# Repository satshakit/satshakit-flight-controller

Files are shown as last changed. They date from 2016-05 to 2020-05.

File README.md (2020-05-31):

<h1 style="font-family: courier;" align="center"> satshakit flight controller</h1>
<p align="center">
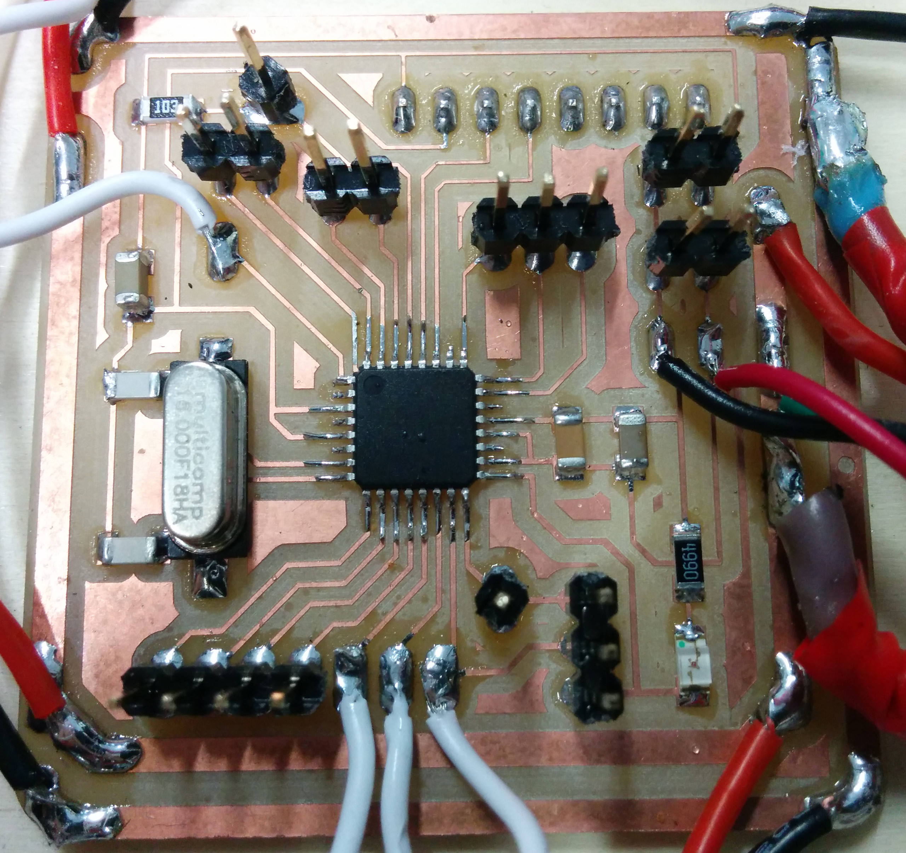
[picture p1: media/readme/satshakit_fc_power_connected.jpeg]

<div align="center"><i>An open source & easy to make flight controller board.</i></div>
</p>  

satshakit flight controller
--
satshakit flight controller is an **open source, MultiWii compatible, flight controller board**, that is possibile to **make in a FabLab**. The design derives from both a **satshakit board** and dual processor flight controller of my **[FabAcademy2015 final project](http://fabacademy.org/archives/2015/eu/students/ingrassia.daniele/index.html)**.

Here you can find all of the satshakit boards: **[satshakit organization](https://github.com/satshakit)**.

Features
--

satshakit flight controller has been designed aiming to be **easy to make, program and use**, so to be possible to **replicate and customize it** in any other Fab Lab. It has the following features:

- support for [any drone configuration](http://www.multiwii.com/connecting-elements) up to **8 motors**
- support for up to **6 channels** receivers 
- costs about **8€**
- **16mhz crystal** for precise clock, reliability and compatibility
- size of **48x48mmm** to fit the size of commercial available boards
- embedded **power board** (if needed)
- possibility to connect and use **any IMU working at 5V**

You can use satshakit flight controller in **DIY drones** or, due the dimensions are the same or less of most of the MultiWii commercial flight controller boards (50x50mmm), as a **replacement flight controller for commercial drones**. For drones up to 4 motors and 15A ESCs, is possible to use the **embedded power board**, otherwise is recommended to use an external power board, and to make the satshakit flight controller without the power board embedded.

Getting started
--

After you finish to solder a satshakit flight controller board, you need to **set its fuses and to program it with MultiWii**. To set the fuses you can easily upload the Arduino Bootloader using Arduino IDE and an **Arduino as ISP**. To do so first upload the Arduino as ISP sketch into an Arduino, and then connect the satshakit flight controller as following (this is the same for the version with the power board and without):

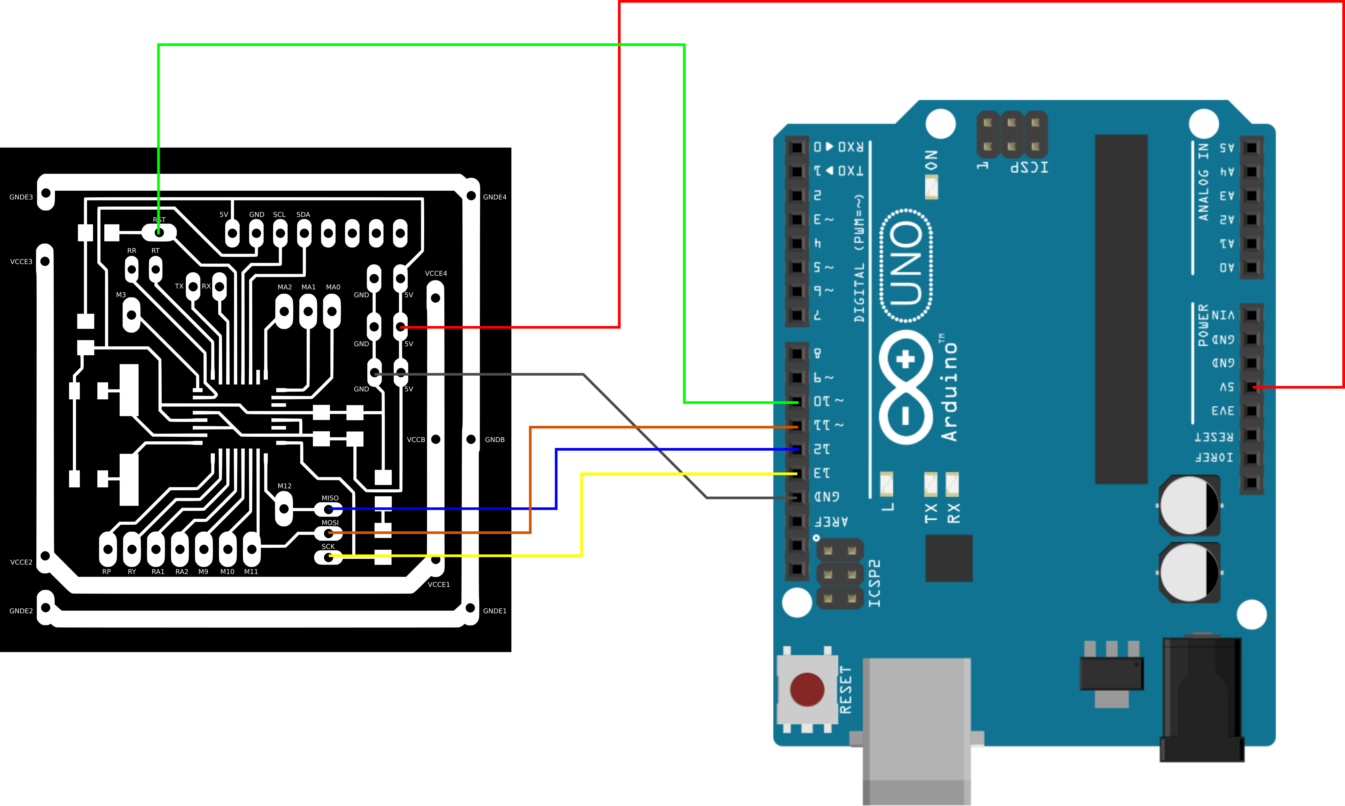
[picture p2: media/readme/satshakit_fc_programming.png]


Once everything is connected, follow these steps to upload Arduino bootloader:

1. open Arduino IDE
2. select proper programmer (for example Arduino as ISP or USBtinyISP)
3. select Arduino UNO as board
4. click on tools->Burn Bootloader

Now you can use again the same connections, Arduino as ISP and Arduino IDE  to **upload your favourite MultiWii** version, this time using **File->Upload using a programmer**.

To connect all the elements fo your drone, you can follow the **satshakit flight controller pinout**:

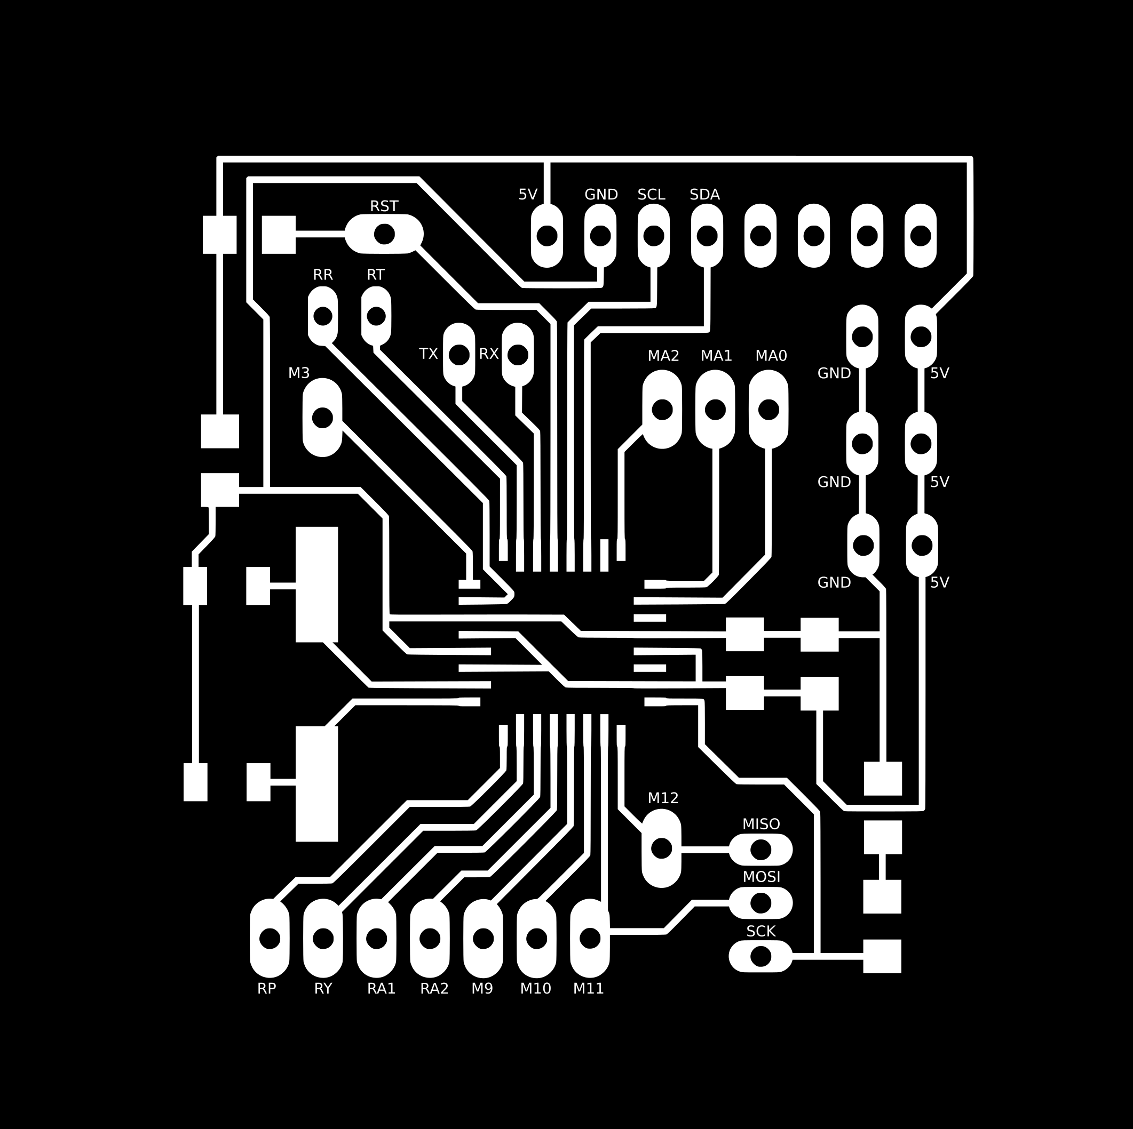
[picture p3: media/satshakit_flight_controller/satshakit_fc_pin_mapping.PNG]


satshakit flight controller pinout with **embedded power power board:**

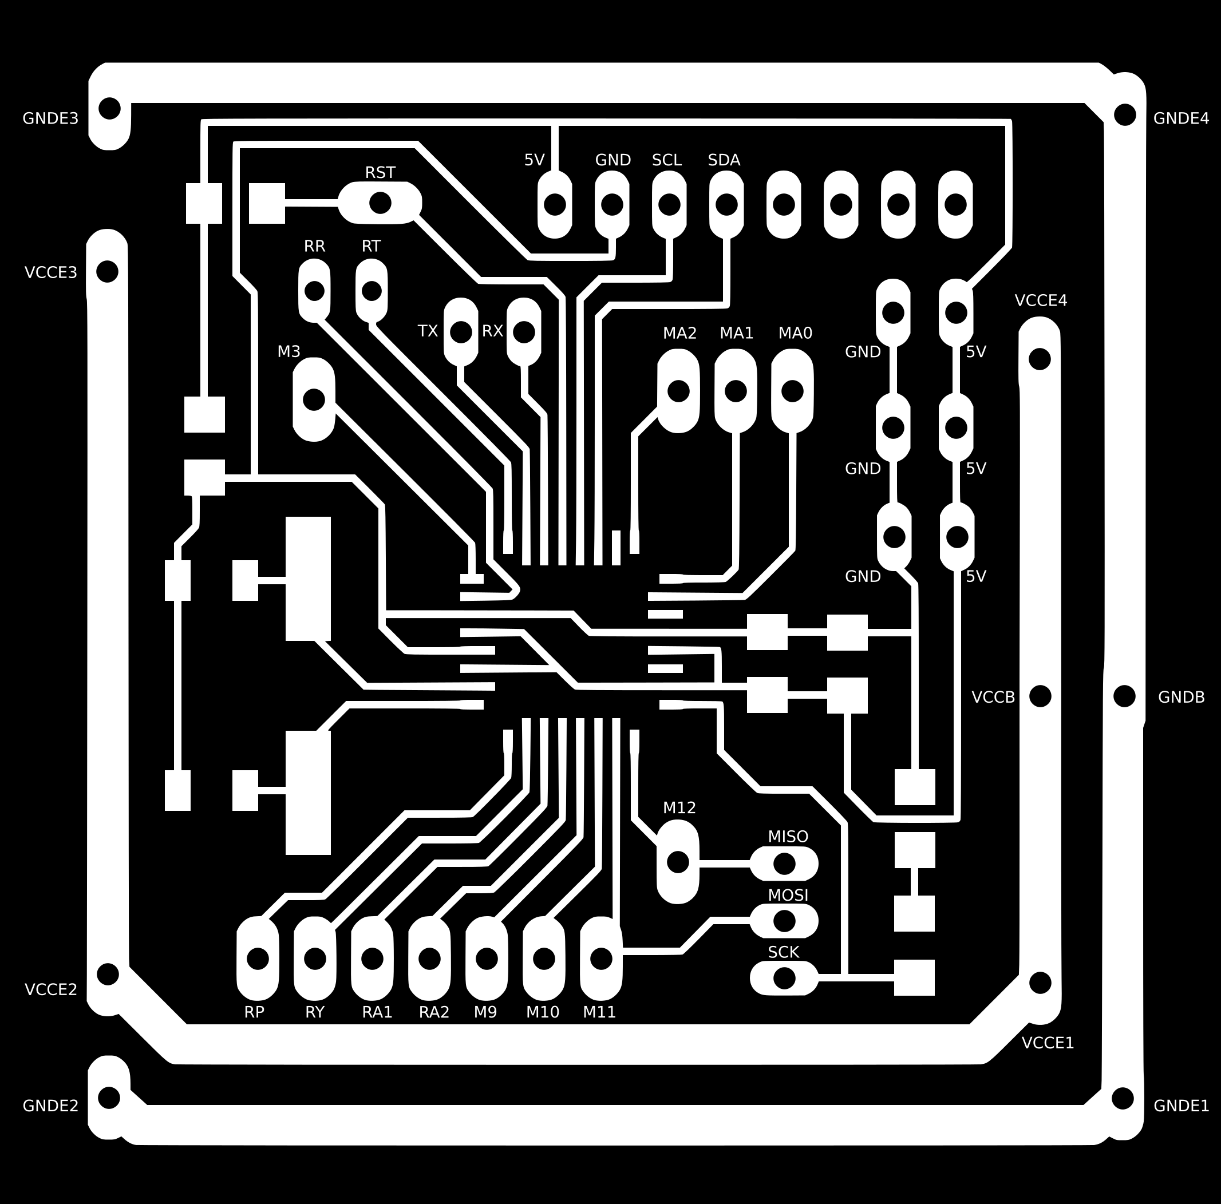
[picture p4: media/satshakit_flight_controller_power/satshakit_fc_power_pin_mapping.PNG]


Downloads
--

**downloads (right click, download as)**

- [satshakit flight controller sch](https://raw.githubusercontent.com/satshakit/satshakit-flight-controller/master/eagle_projects/satshakit_flight_controller/satshakit_fc.sch)
- [satshakit flight controller brd](https://raw.githubusercontent.com/satshakit/satshakit-flight-controller/master/eagle_projects/satshakit_flight_controller/satshakit_fc.brd)
- [satshakit flight controller svg](https://raw.githubusercontent.com/satshakit/satshakit-flight-controller/master/media/satshakit_flight_controller/satshakit_fc.svg)
- [satshakit flight controller internal](https://raw.githubusercontent.com/satshakit/satshakit-flight-controller/master/media/satshakit_flight_controller/satshakit_fc_internal.png)
- [satshakit flight controller holes](https://raw.githubusercontent.com/satshakit/satshakit-flight-controller/master/media/satshakit_flight_controller/satshakit_fc_holes.png)
- [satshakit flight controller cut](https://raw.githubusercontent.com/satshakit/satshakit-flight-controller/master/media/satshakit_flight_controller/satshakit_fc_cut.png)
- [satshakit flight controller cut tip](https://raw.githubusercontent.com/satshakit/satshakit-flight-controller/master/media/satshakit_flight_controller/satshakit_fc_cut_tip.png)
- [satshakit flight controller with power board sch](https://raw.githubusercontent.com/satshakit/satshakit-flight-controller/master/eagle_projects/satshakit_flight_controller_power/satshakit_fc_power.sch)
- [satshakit flight controller with power board brd](https://raw.githubusercontent.com/satshakit/satshakit-flight-controller/master/eagle_projects/satshakit_flight_controller_power/satshakit_fc_power.brd)
- [satshakit flight controller with power board svg](https://raw.githubusercontent.com/satshakit/satshakit-flight-controller/master/media/satshakit_flight_controller_power/satshakit_fc_power.svg)
- [satshakit flight controller with power board internal](https://raw.githubusercontent.com/satshakit/satshakit-flight-controller/master/media/satshakit_flight_controller_power/satshakit_fc_power_internal.png)
- [satshakit flight controller with power board holes](https://raw.githubusercontent.com/satshakit/satshakit-flight-controller/master/media/satshakit_flight_controller_power/satshakit_fc_power_holes.png)
- [satshakit flight controller with power board cut](https://raw.githubusercontent.com/satshakit/satshakit-flight-controller/master/media/satshakit_flight_controller_power/satshakit_fc_power_cut.png)
- [satshakit flight controller with power board cut tip](https://raw.githubusercontent.com/satshakit/satshakit-flight-controller/master/media/satshakit_flight_controller_power/satshakit_fc_power_cut_tip.png)
- [satshakit flight controller BOM xlsx](https://raw.githubusercontent.com/satshakit/satshakit-flight-controller/master/docs/satshakit_fc_BOM.xlsx)
- [satshakit flight controller BOM ods](https://raw.githubusercontent.com/satshakit/satshakit-flight-controller/master/docs/satshakit_fc_BOM.ods)

Media
--

board, soldered and installed satshakit flight controller:

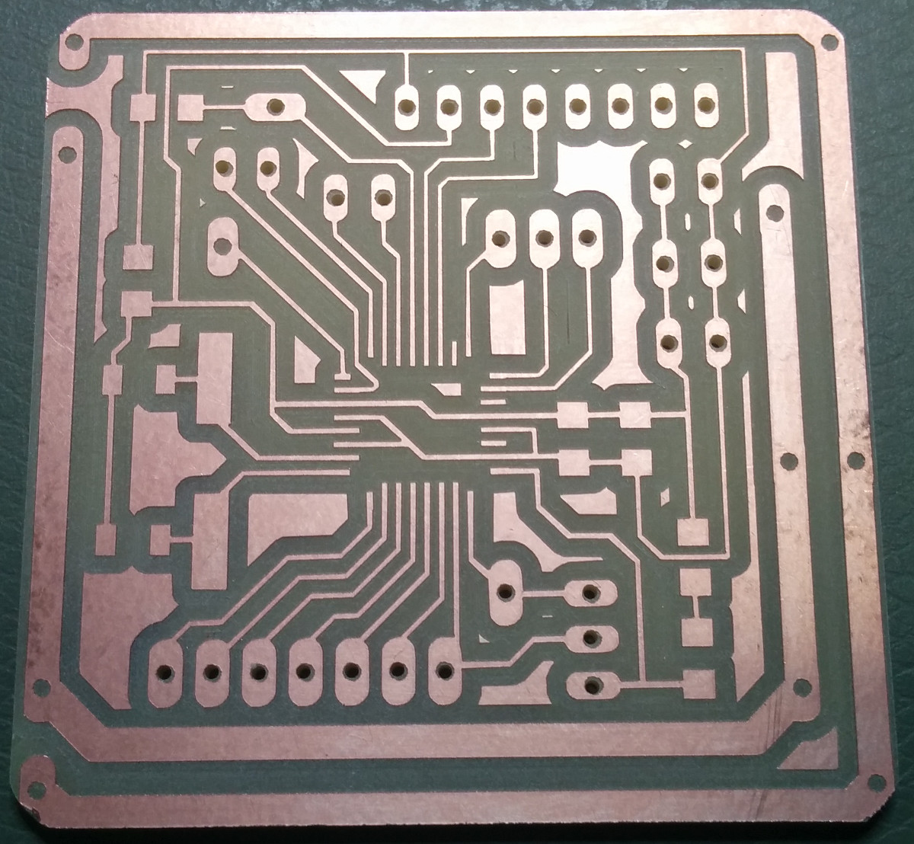
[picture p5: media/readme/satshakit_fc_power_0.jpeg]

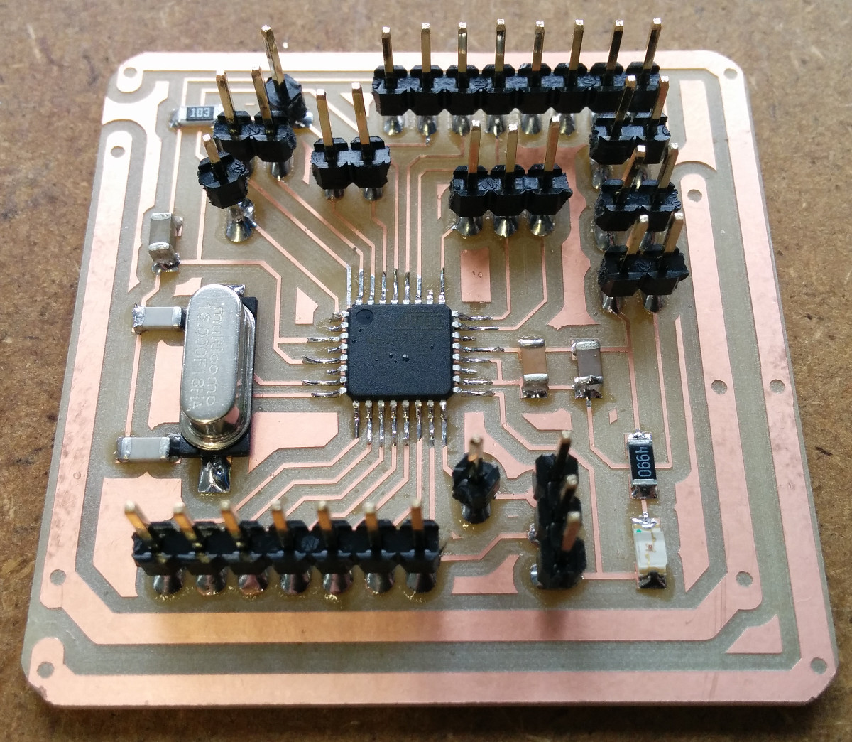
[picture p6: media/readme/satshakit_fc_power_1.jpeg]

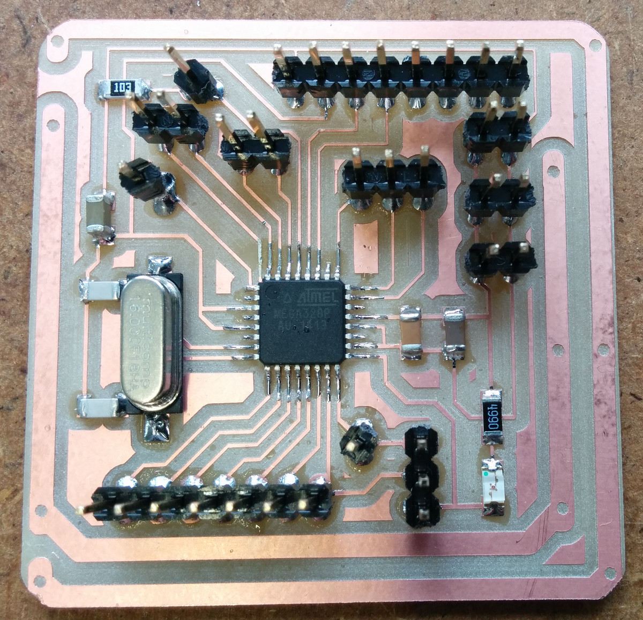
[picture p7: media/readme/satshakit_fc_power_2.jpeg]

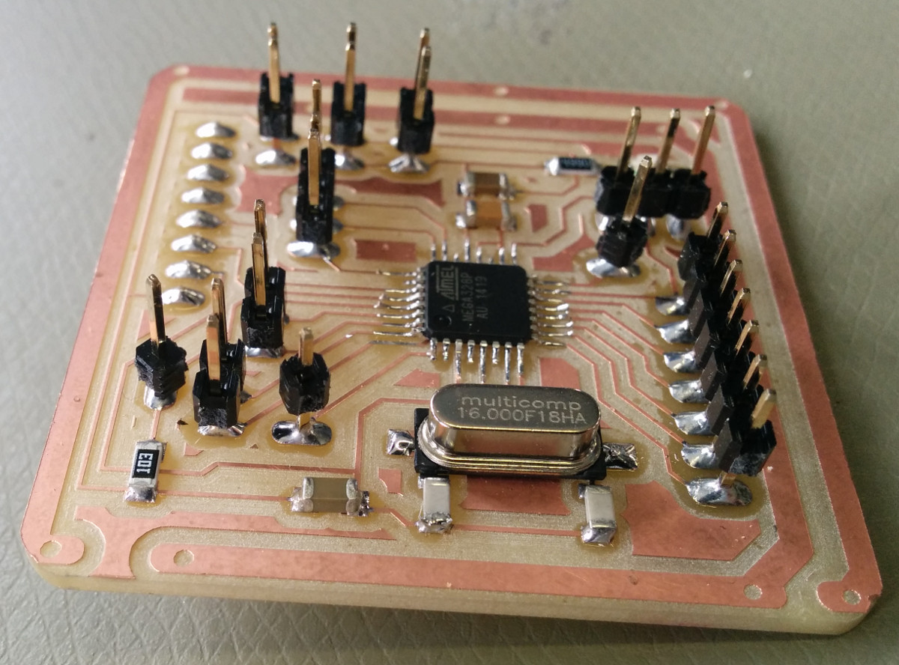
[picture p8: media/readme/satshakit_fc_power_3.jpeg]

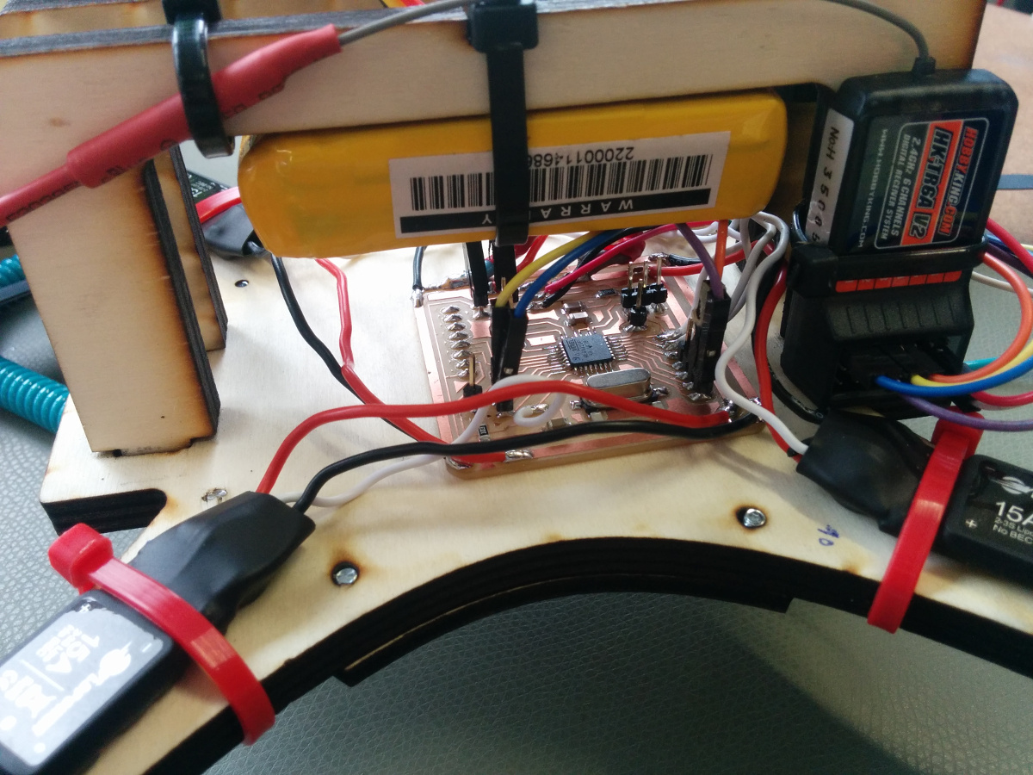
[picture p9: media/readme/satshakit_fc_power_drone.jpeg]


uploading Arduino bootloader:

<a href="http://www.youtube.com/watch?feature=player_embedded&v=8BaBp0zfSmk
" target="_blank"></a>

uploading Multiwii:

<a href="http://www.youtube.com/watch?feature=player_embedded&v=ZrNh0s9pX4o
" target="_blank"></a>

Multiwii test:

<a href="http://www.youtube.com/watch?feature=player_embedded&v=WtUbjrxpeHY
" target="_blank"></a>

What's in the repo
--

- **[docs](https://github.com/satshakit/satshakit-flight-controller/tree/master/docs)**: BOM files for Farnell
- **[egle projects](https://github.com/satshakit/satshakit-flight-controller/tree/master/eagle_projects)**: eagle projects of the satshakit flight controller
- **[media](https://github.com/satshakit/satshakit-flight-controller/tree/master/media)**: svgs, connections schemas, images for cnc milling machine, other images

Authors
--

- Daniele Ingrassia

Contact
--

- **ingrassiada@gmail.com**
- **[linkedin](http://it.linkedin.com/in/danieleingrassia)**

Thanks
--

[Fablab Kamp-Lintfort](http://fablab.hochschule-rhein-waal.de/index.php/de/)<br />
Hochschule Rhein-Waal<br />
Friedrich-Heinrich-Allee 25, 47475 Kamp-Lintfort, Germany<br />
fablab@hochschule-rhein-waal.de

License
--
This work is licensed under the terms of the open source license: Creative Commons Attribution-ShareAlike 4.0 International ([CC BY-SA 4.0](https://creativecommons.org/licenses/by-sa/4.0/)).

Disclaimer  
--

<div class="align-justify">
This hardware/software is provided "as is", and you use the hardware/software at your own risk. Under no circumstances shall any author be liable for direct, indirect, special, incidental, or consequential damages resulting from the use, misuse, or inability to use this hardware/software, even if the authors have been advised of the possibility of such damages.</div>

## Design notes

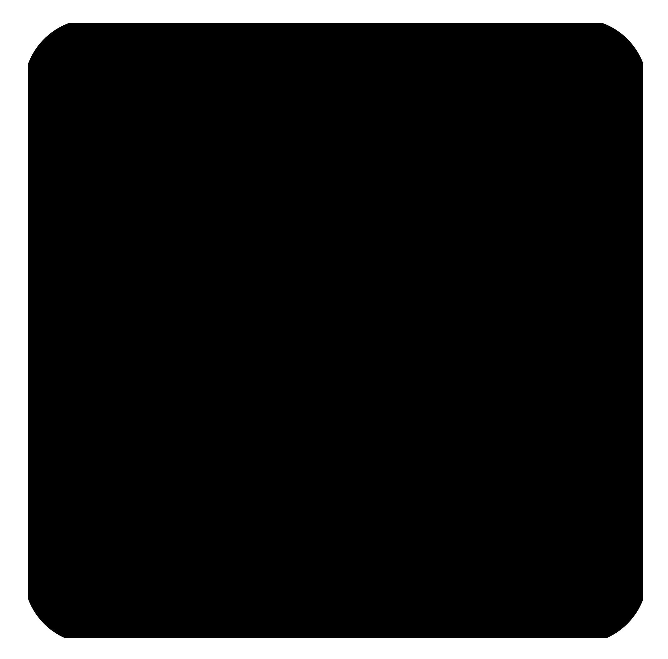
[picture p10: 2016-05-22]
media/satshakit_flight_controller_power/satshakit_fc_power_cut.png

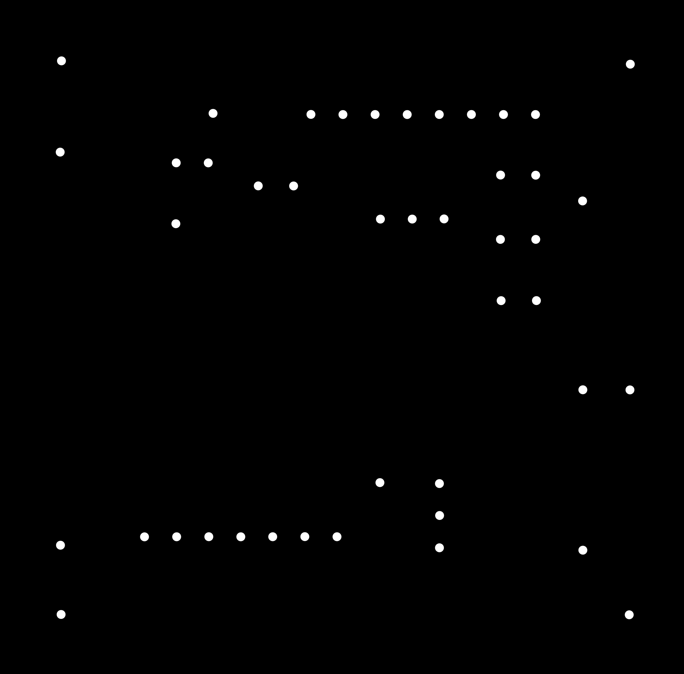
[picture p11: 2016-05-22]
media/satshakit_flight_controller_power/satshakit_fc_power_holes.png

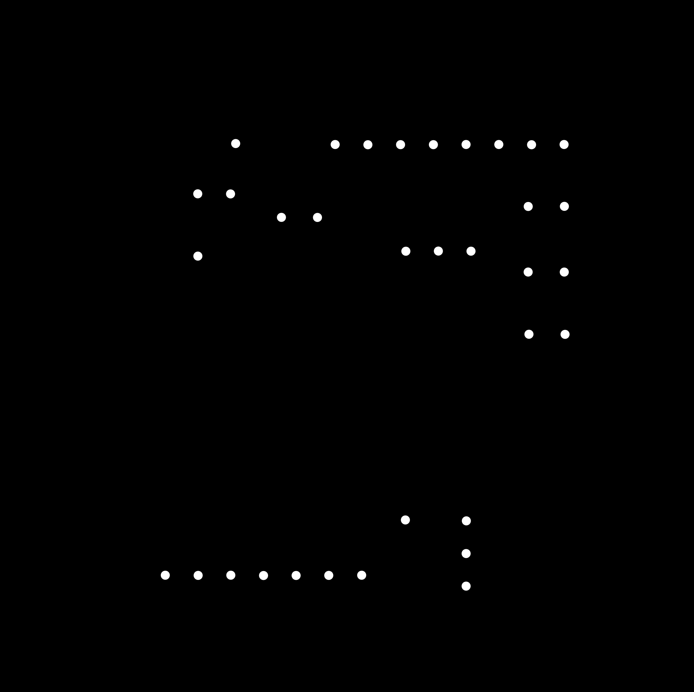
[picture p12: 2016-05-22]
media/satshakit_flight_controller/satshakit_fc_holes.png

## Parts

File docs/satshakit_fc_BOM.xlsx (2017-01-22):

Value | Manufacturer Part No | Package | Description | FARNELL | Price € | Quantity | Min. Quantity Cost €
- | ATMEGA328P-AU | TQFP-32 | microcontroller | 1715486 (http://it.farnell.com/atmel/atmega328p-au/mcu-8bit-atmega-20mhz-tqfp-32/dp/1715486) | 2.78 | 1 | 2.78
16Mhz/18pF | MCRSD16000F183000RR | SMD 11.4 x 4.7 mm | crystal | 2395958 (http://it.farnell.com/multicomp/mcrsd16000f183000rr/crystal-16mhz-18pf-hc49-us-smd/dp/2395958) | 0.20 | 1 | 0.20
yellow | MCL-S250YC | 1206 | yellow led | 1581231 (http://it.farnell.com/multicomp/mcl-s250yc/led-smd-1206-giallo/dp/1581231) | 0.05 | 1 | 0.26
10K | ERJ8GEYJ103V | 1206 | resistor | 2057856 (http://it.farnell.com/panasonic-electronic-components/erj8geyj103v/resistore-1206-10k-5-0-25w/dp/2057856) | 0.03 | 1 | 0.26
499 | CRCW1206499RFKEA | 1206 | resistor | 1470020 (http://it.farnell.com/vishay-draloric/crcw1206499rfkea/resistor-1206-499r-1/dp/1470020) | 0.03 | 1 | 0.28
22pF | MC1206N220J500CT | 1206 | capacitor | 2320891 (http://it.farnell.com/multicomp/mc1206n220j500ct/condens-mlcc-c0g-np0-22pf-50v/dp/2320891) | 0.05 | 2 | 0.47
10uF | MC1206X106K250CT | 1206 | capacitor | 2112753 (http://it.farnell.com/multicomp/mc1206x106k250ct/condensatore-mlcc-x5r-10uf-25v/dp/2112753) | 0.15 | 1 | 0.15
1uF | MC1206F105Z500CT | 1206 | capacitor | 1759455 (http://it.farnell.com/multicomp/mc1206f105z500ct/condensatore-mlcc-y5v-1uf-50v/dp/1759455) | 0.06 | 1 | 0.63
100nF | MC1206B104K500CT | 1206 | capacitor | 1759361 (http://it.farnell.com/multicomp/mc1206b104k500ct/condensatore-mlcc-x7r-100nf-50v/dp/1759361) | 0.04 | 1 | 0.35
- | 61304011021 | 2.54 mm | pin header | 2356192 (http://it.farnell.com/wurth-elektronik/61304011021/header-2-54mm-pin-tht-r-a-40way/dp/2356192) | 1.77 | 1 | 1.77
- | M20-9990246 | 2.54 mm | pin header | 1022247 (http://it.farnell.com/harwin/m20-9990246/header-diritta-2-54mm-1row-bifase/dp/1022247) | 0.07 | 1 | 0.65
 |  |  |  |  |  |  | Total cost
 |  |  |  |  |  |  | 7.81

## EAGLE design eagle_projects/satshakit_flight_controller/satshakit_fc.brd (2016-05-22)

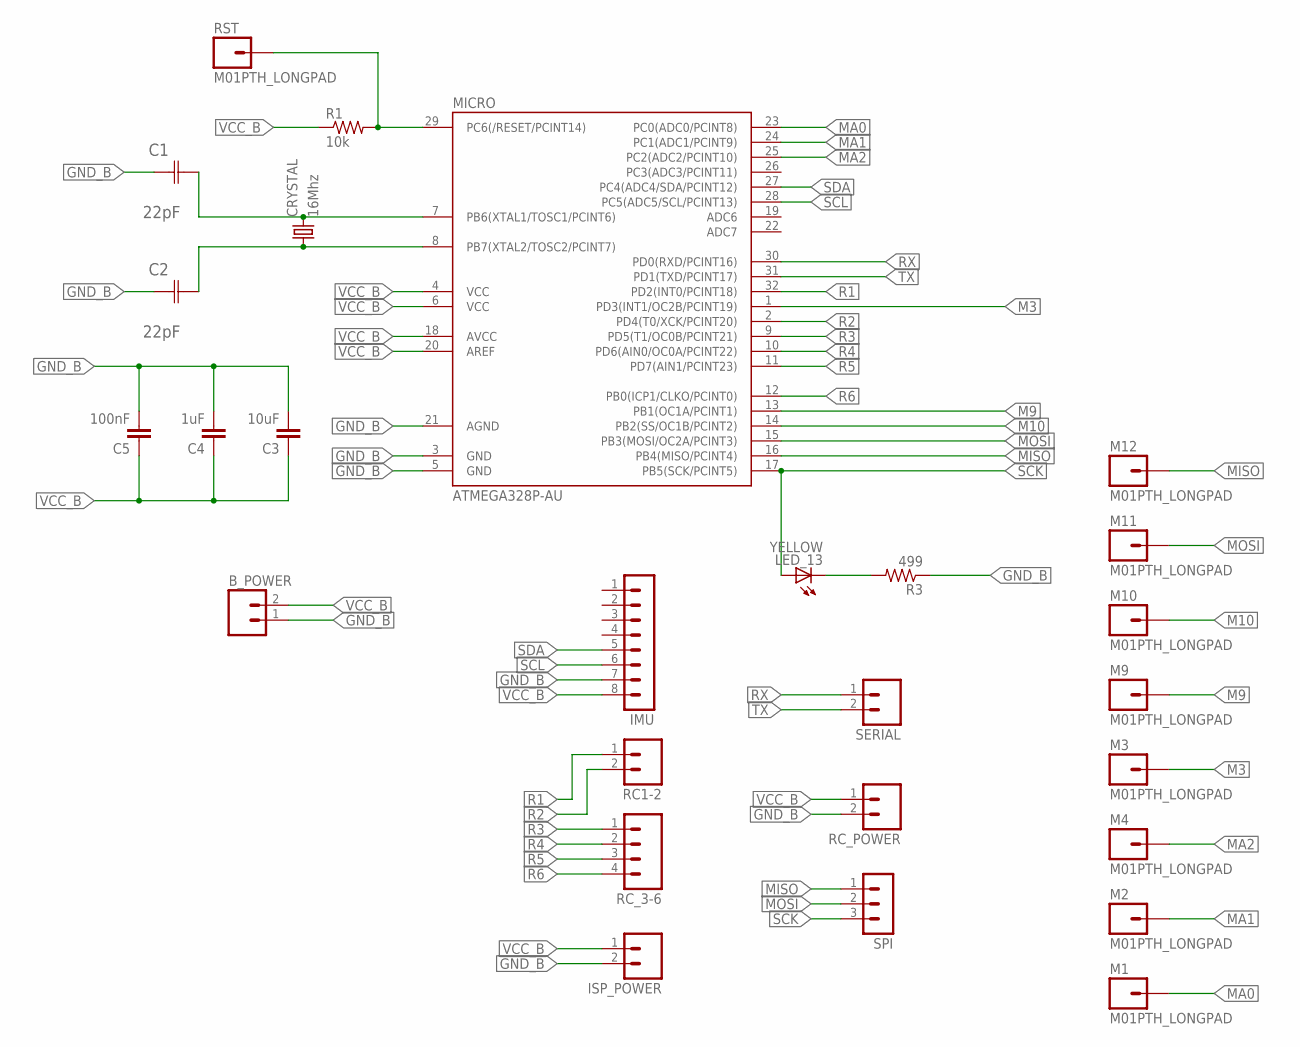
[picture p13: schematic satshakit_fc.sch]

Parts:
B_POWER: M02LOCK_LONGPADS; 1X02_LOCK_LONGPADS
C1, C2: 22pF; CAPC3216X178N
C3: 10uF; 1206
C4: 1uF; 1206
C5: 100nF; 1206
CRYSTAL: 16Mhz; CSM-7X-DU
IMU: MA08-1
ISP_POWER: M02LOCK_LONGPADS; 1X02_LOCK_LONGPADS
LED_13: YELLOW; 1206
M1, M2, M3, M4, M9, M10, M11, M12: M01PTH_LONGPAD; 1X01_LONGPAD
MICRO: ATMEGA328P-AU; TQFP32-08
R1: 10k; 1206
R3: 499; 1206
RC1-2: M02; 02P
RC_3-6: M04LONGPADS; 1X04_LONGPADS
RC_POWER: M02LOCK_LONGPADS; 1X02_LOCK_LONGPADS
RST: M01PTH_LONGPAD; 1X01_LONGPAD
SERIAL: M02LOCK_LONGPADS; 1X02_LOCK_LONGPADS
SPI: MA03-1

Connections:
GND_B: B_POWER.1, C1.1 (C1), C2.1 (C1), C3.2, C4.2, C5.2, IMU.7, ISP_POWER.2, MICRO.3 (GND), MICRO.5 (GND), MICRO.21 (AGND), R3.1, RC_POWER.2
M3: M3.1, MICRO.1 (PD3(INT1/OC2B/PCINT19))
M9: M9.1, MICRO.13 (PB1(OC1A/PCINT1))
M10: M10.1, MICRO.14 (PB2(SS/OC1B/PCINT2))
MA0: M1.1, MICRO.23 (PC0(ADC0/PCINT8))
MA1: M2.1, MICRO.24 (PC1(ADC1/PCINT9))
MA2: M4.1, MICRO.25 (PC2(ADC2/PCINT10))
MISO: M12.1, MICRO.16 (PB4(MISO/PCINT4)), SPI.1
MOSI: M11.1, MICRO.15 (PB3(MOSI/OC2A/PCINT3)), SPI.2
unnamed: C1.2 (C2), CRYSTAL.2, MICRO.7 (PB6(XTAL1/TOSC1/PCINT6))
unnamed: MICRO.29 (PC6(/RESET/PCINT14)), R1.2, RST.1
unnamed: C2.2 (C2), CRYSTAL.1, MICRO.8 (PB7(XTAL2/TOSC2/PCINT7))
unnamed: LED_13.2 (C), R3.2
R1: MICRO.32 (PD2(INT0/PCINT18)), RC1-2.1
R2: MICRO.2 (PD4(T0/XCK/PCINT20)), RC1-2.2
R3: MICRO.9 (PD5(T1/OC0B/PCINT21)), RC_3-6.1
R4: MICRO.10 (PD6(AIN0/OC0A/PCINT22)), RC_3-6.2
R5: MICRO.11 (PD7(AIN1/PCINT23)), RC_3-6.3
R6: MICRO.12 (PB0(ICP1/CLKO/PCINT0)), RC_3-6.4
RX: MICRO.30 (PD0(RXD/PCINT16)), SERIAL.1
SCK: LED_13.1 (A), MICRO.17 (PB5(SCK/PCINT5)), SPI.3
SCL: IMU.6, MICRO.28 (PC5(ADC5/SCL/PCINT13))
SDA: IMU.5, MICRO.27 (PC4(ADC4/SDA/PCINT12))
TX: MICRO.31 (PD1(TXD/PCINT17)), SERIAL.2
VCC_B: B_POWER.2, C3.1, C4.1, C5.1, IMU.8, ISP_POWER.1, MICRO.4 (VCC), MICRO.6 (VCC), MICRO.18 (AVCC), MICRO.20 (AREF), R1.1, RC_POWER.1

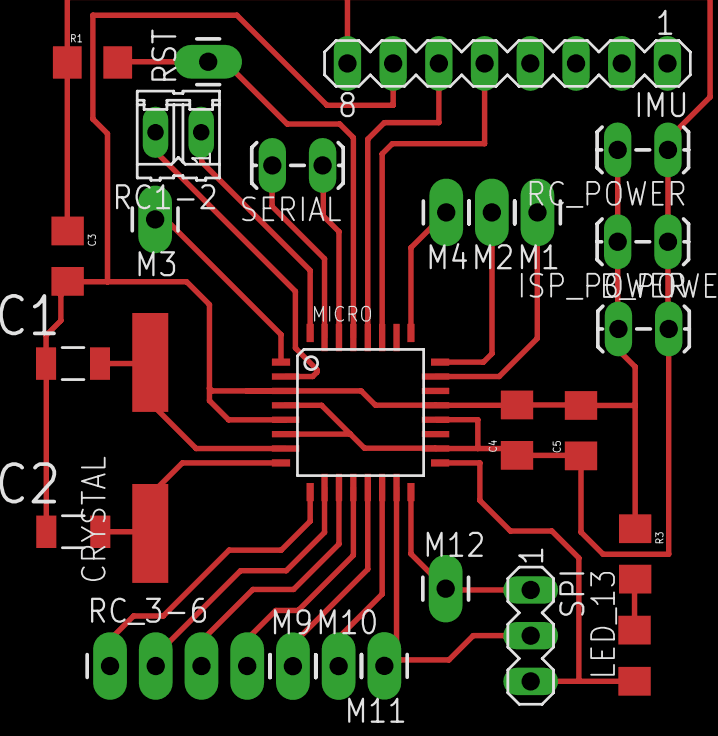
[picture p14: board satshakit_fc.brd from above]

Board: 2 copper layers, 27 parts (0 on the bottom side), 25 nets.

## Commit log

2016-05-22 first commit of satshakit flight controller
    [satshakit_BOM.xlsx, satshakit_fc.brd, satshakit_fc.sch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]
2017-01-22 fixed BOM links
    [satshakit_fc_BOM.xlsx]
2017-01-22 fixed BOM
    [satshakit_fc_BOM-.xlsx, satshakit_fc_BOM.xlsx]
2017-01-22 removed the satshakit boards list

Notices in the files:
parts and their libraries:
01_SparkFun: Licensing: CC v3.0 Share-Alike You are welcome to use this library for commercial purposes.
